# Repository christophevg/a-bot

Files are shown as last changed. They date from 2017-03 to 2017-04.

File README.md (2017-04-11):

# A-Bot
Een eigen kleine programmeerbare, zelf-rijdende robot maken.  
[http://knutselbaar.be/projecten/A-Bot](http://knutselbaar.be/projecten/A-Bot)

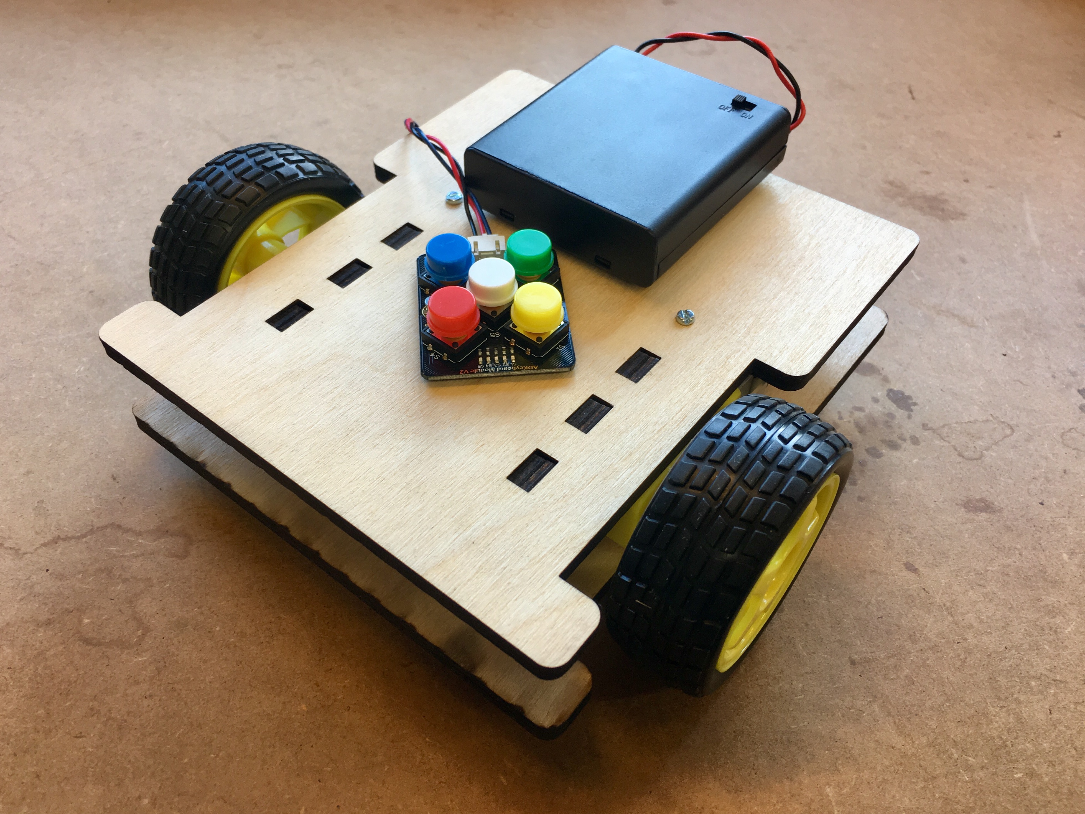
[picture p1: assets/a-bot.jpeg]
A-Bot

<p align="right">A-Bot versie 1</p>

## Inleiding

Tijdens een bezoek aan [Technolopis](http://technopolis.be) ontdekte onze zoon Arjen, 5 jaar, de [Bee Bot](https://www.bee-bot.us). Een zeer eenvoudige, programmeerbare, zelf-rijdende robot.

Via enkele knoppen kan deze robot geprogrammeerd worden om rond te rijden: rechtdoor, rechts/links draaien,... Op die manier kunnen kinderen eenvoudig leren om via elementaire ruimtelijke instructies de robot een parcours af te laten leggen.

Je kan deze bots kopen, voor ongeveer 80 euro, maar... je kan dit ook vrij eenvoudig zelf maken. Er bestaan zelfs veel kits van gelijkaardige robots, maar... je kan dit ook vrij eenvoudig zelf maken :-)

Dit project is bedoeld om te tonen hoe je dit kan doen en hoe je dus naast veel plezier met de robot zelf, ook heel veel plezier kan hebben om te leren hoe je dit zelf kan bouwen.

Er zijn verschillende aspecten aan: enerzijds de constructie van de robot en anderzijds de programmatie om hem echt tot leven te brengen.

### In deze _repository_

...verzamelen we alle bestanden, documenten, tekeningen, ontwerpen die we maken om de E-Liner te ontwerpen, alsook de software die we er op zetten om hem te laten rijden en te programmeren.

## Versie 1

### Onderdelen

Voor de eerste versie van de A-Bot vertrekken we van een [Particle Photon](https://www.particle.io/products/hardware/photon-wifi-dev-kit). Dit is een Arduino-achtige microcontroller met WiFi en een fantastisch online platform om er mee te werken.

Als aandrijving vertrekken we van een paar eenvoudige DC motoren. Om deze makkelijk aan te sturen, gebruiken we bijkomende chip: de L293. Om de motoren iets beter te kunnen controleren, voegen we ook een _encoder_ toe. 

Een balwiel, enkele knoppen en een batterijbox, maken onze onderdelen lijst compleet.

* 1 x [Particle Photon](https://www.antratek.be/photon) (~&euro;24)
* 1 x set [DC motoren en wielen](https://iprototype.nl/products/robotics/servo-motors/motors-wheels) (~&euro;18)
* 1 x [L293DNE](https://iprototype.nl/products/components/ics/motorcontroller-chip-L293D) (~&euro;5,15)
* 1 x set [Encoders voor DC motor](https://iprototype.nl/products/robotics/misc/dc-motor-encoder) (~&euro;15,50)
* 1 x [Gravity Keypad](https://iprototype.nl/products/components/buttons-switches/gravity-keypad) (~&euro;8)
* 1 x [Ball caster](https://iprototype.nl/products/robotics/misc/ball-caster-30mm) (~&euro;2,30)
* 1 x [Batterijbox 4xAA](https://iprototype.nl/products/accessoires/power/battery-box-4xAA) (~&euro;4,75)

### Chassis Design

Om al deze onderdelen samen te brengen tot een robotje, snijden we uit hout (of plexi) enkele delen met behulp van een laser cutter:

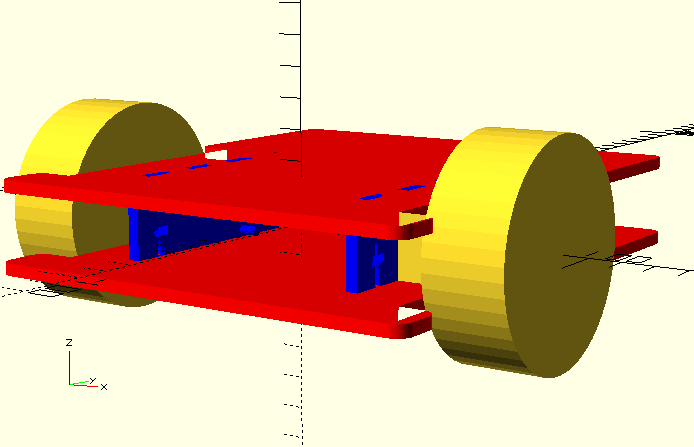
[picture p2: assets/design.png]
Design


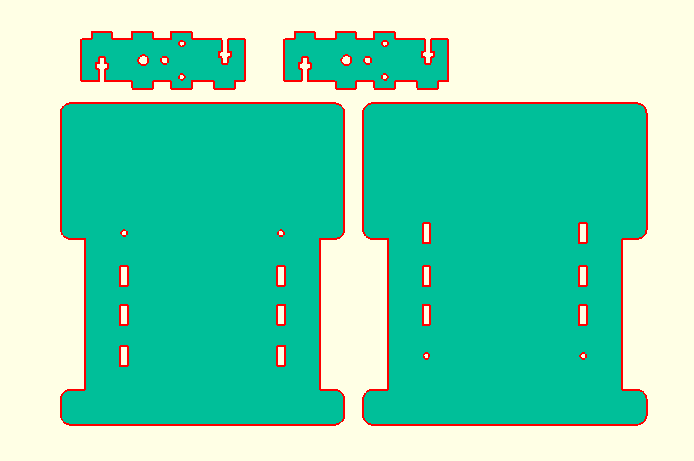
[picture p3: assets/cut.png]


### Electronica & Software

In verschillende stappen kan je zelf je A-Bot opbouwen:

1. [Blink](src/blink/) - Dit is de eenvoudigste test om te controleren dat alles werkt. Het laat de ingebouwde blauwe LED van de Photon blinken.
2. [Motor](src/motor/) - Dit is de basis opstelling voor het aansturen van een motor.
3. [Encoder](src/encoder/) - Dit is de basis opstelling voor het uitlezen van een encoder.
4. [Keypad](src/keypad/) - Dit is de basis opstelling voor het uitlezen van het keypad. 
5. [A-Bot](src/a-bot/) - Deze applicatie brengt alle onderdelen van de A-Bot samen tot een programmeerbaar robotje.

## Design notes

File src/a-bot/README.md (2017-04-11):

# A-Bot

Deze applicatie brengt alle onderdelen van de A-Bot samen tot een programmeerbaar robotje.

A-Bot

## Wat moet je bouwen?

Als we nu 2 [motoren](../motor/), 2 [encoders](../encoder/) en 1 [keypad](../keypad/) samenbrengen en zelf eventueel een _gaatjesprint_ maken, bekom je de volledige electronica die je nodig hebt:

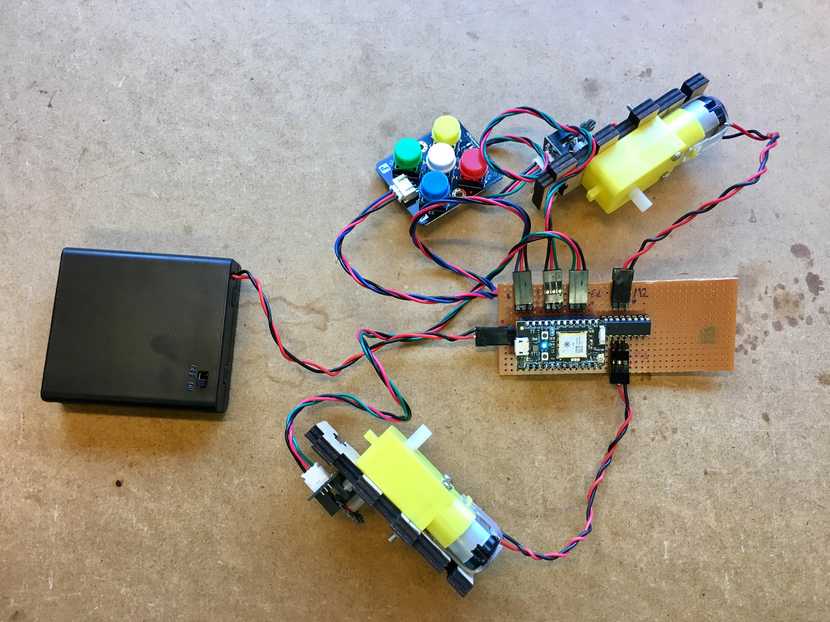
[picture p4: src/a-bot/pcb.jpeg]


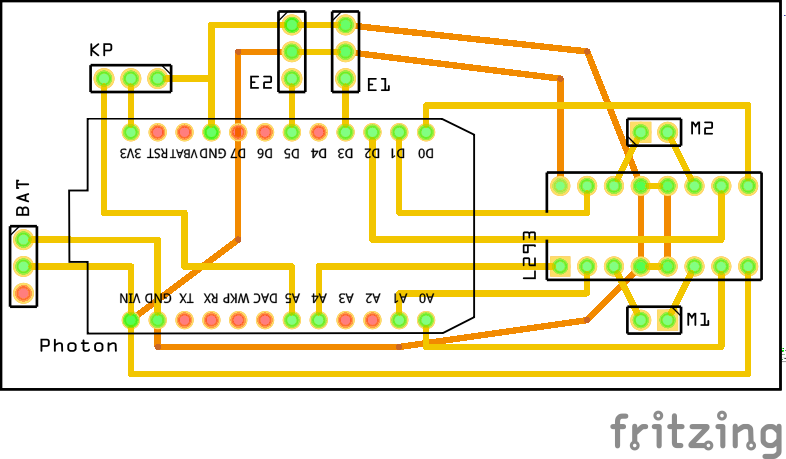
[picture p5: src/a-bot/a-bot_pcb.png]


Als je andere pinnen van de Photon gebruikt, kan je dit in [`config.h`](config.h) configureren.

## Hoe doe je dit werken op de Photon?

Vanuit de `src/` folder, geef je het commando `make`:

```bash
$ PROJECT=a-bot make
*** Compileren en flashen van a-bot
particle flash 2b002f001147333439313830 a-bot
Including:
    a-bot/config.h
    a-bot/a-bot.ino
attempting to flash firmware to your device 2b002f001147333439313830
Flash device OK:  Update started
*** Start van console uitvoer. Beëindig met 'Ctrl+a k y'.
    Druk op een toets om verder te gaan...
```

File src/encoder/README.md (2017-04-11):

# Encoder

Dit is de basis opstelling voor het uitlezen van een encoder.

## Wat moet je bouwen?

Dit voorbeeld bouwt voort op het voorbeeld voor de [motor](../motor/). Op de [wiki van DFRobot](https://www.dfrobot.com/wiki/index.php/Wheel_Encoders_for_DFRobot_3PA_and_4WD_Rovers_(SKU:SEN0038)) vind je informatie hoe je de encoder op de motor kan aansluiten.

De gebruikte motoren verschillen echter een beetje en vragen wat knutselwerk. De opstelling van het chassis laat echter toe om de encoder op de vertikale steunen te bevestigen nadat de motoren langs de andere kant van de steun bevestigd is.

(_foto's volgen_)

## Hoe werkt dit?

Een encoder bestaat uit een getand wieltje en een lichtsensor. Wanneer het wieltje met de as van de motor ronddraait zullen de tandjes het licht afwisselend doorlaten of tegenhouden.

De encoder vraagt een 5V voeding en geeft een digitaal signaal terug dat aangeeft of de encoder licht detecteert of niet. Zo kunnen we het aantal tandjes dat ronddraaien tellen.

## Hoe doe je dit werken op de Photon?

Vanuit de `src/` folder, geef je het commando `make`:

```bash
$ PROJECT=encoder make
*** Compileren en flashen van encoder
particle flash 2b002f001147333439313830 encoder
Including:
    encoder/encoder.ino
attempting to flash firmware to your device 2b002f001147333439313830
Flash device OK:  Update started
*** Start van console uitvoer. Beëindig met 'Ctrl+a k y'.
    Druk op een toets om verder te gaan...
```

Op de console toont de applicatie telkens het aantal stappen dat geteld werd gedurende 2 seconden.

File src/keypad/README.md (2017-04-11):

# Keypad

Dit is de basis opstelling voor het uitlezen van het keypad.

## Wat moet je bouwen?

De encoder wordt aangesloten met drie draden: 2 daarvan dienen voor de stroomvoorziening en de derde geeft een signaal terug dat aangeeft welke knop ingeduwd wordt.

Volgens de documentatie van het keypad, werkt dit op 5V. De Photon wordt wel gevoed met 5V, maar werkt voor de rest hoofdzakelijk op 3.3V. Als we naar de [samenstelling](https://iprototype.nl/docs/gravity-keypad-schema.pdf) van het keypad kijken, zien we dat de knoppen met verschillende weerstanden zorgen voor verschillende spanningen over de uitgaande, derde draad.

Voor dit voorbeeld, sluiten we het keypad dus aan op pinnen `3.3V`, `GND` en `A4`.

## Hoe werkt dit?

In de code bevindt zich 1 functie die de uitgaande spanning van het keypad leest en omzet tot een numerieke aanduiding voor de ingedrukte knop:

```c
#define KNOPPEN A4

uint8_t lees_knoppen() {
  int invoer = 4095 - analogRead(KNOPPEN);
  if(invoer < 200) { return 0; }
  if(invoer < 300) { return 5; }
  if(invoer < 500) { return 4; }
  if(invoer < 645) { return 1; }
  if(invoer < 675) { return 3; }
  if(invoer < 800) { return 2; }
  return 0; // geen knop
}
```

## Hoe doe je dit werken op de Photon?

Vanuit de `src/` folder, geef je het commando `make`:

```bash
$ PROJECT=keypad make
*** Compileren en flashen van keypad
particle flash 2b002f001147333439313830 keypad
Including:
    keypad/keypad.ino
attempting to flash firmware to your device 2b002f001147333439313830
Flash device OK:  Update started
*** Start van console uitvoer. Beëindig met 'Ctrl+a k y'.
    Druk op een toets om verder te gaan...
```

Op de console toont de applicatie de knoppen die ingedrukt worden.

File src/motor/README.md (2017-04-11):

# Motor

Dit is de basis opstelling voor het aansturen van een motor.

## Wat moet je bouwen?

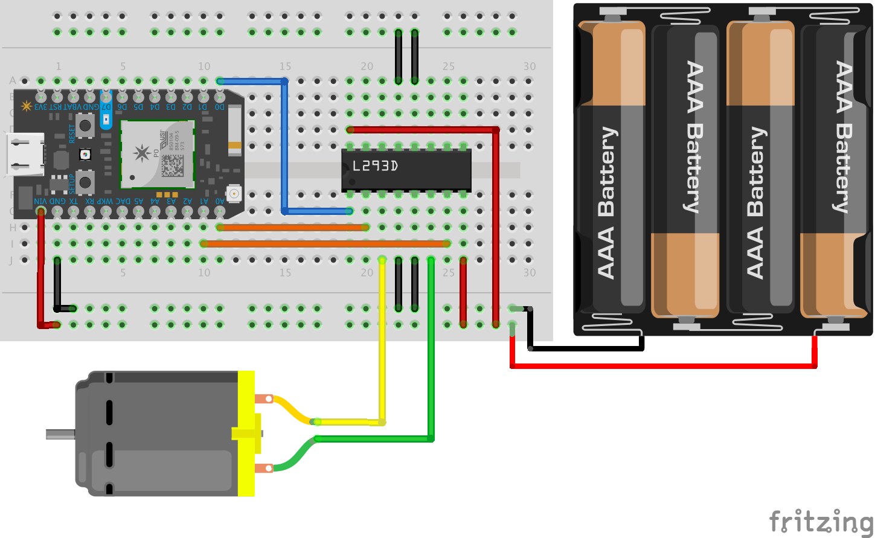
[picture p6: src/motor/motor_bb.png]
Breadboard


De batterijen voorzien de opstelling van iets meer dan 5V. Hiermee wordt (via de rode draden) enerzijds de Photon van stroom voorzien, als ook de L293D.

De L293D wordt aangestuurd met drie draden per motor: 2 draden dienen om de draai-richting aan te geven (oranje) en 1 draad om de snelheid te bepalen (blauw).

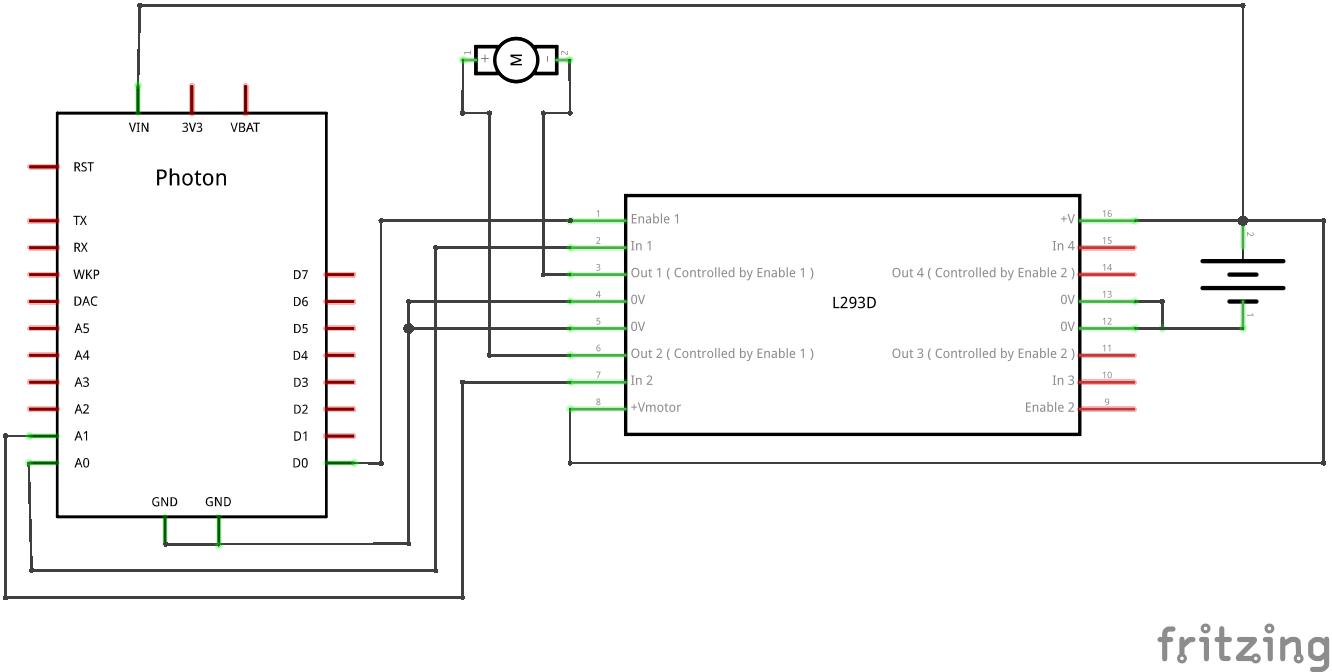
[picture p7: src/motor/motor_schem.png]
Schema


De twee draden waarmee we de draai-richting kunnen aangeven, kunnen samen 4 verschillende situaties aangeven: stilstaan, linksom draaien, rechtsom draaien en remmen.

## Software

In de software zie je één functie die alle logica bevat om een motor aan te sturen:

```c
void motor_update(int16_t snelheid) {
  // houd snelheid binnen grenzen
  if(abs(snelheid) < MIN_SNELHEID) { snelheid = 0; }
  if(abs(snelheid) > MAX_SNELHEID) {
    snelheid = MAX_SNELHEID * (snelheid/abs(snelheid));
  }

  // bepaal draairichting
  if(snelheid == 0) {
    // stop
    digitalWrite(MOTOR1_1A, LOW);
    digitalWrite(MOTOR1_2A, LOW);
  } else if(snelheid < 0) {
    // achterwaarts
    digitalWrite(MOTOR1_1A, HIGH);
    digitalWrite(MOTOR1_2A, LOW);
  } else {
    // voorwaarts
    digitalWrite(MOTOR1_1A, LOW);
    digitalWrite(MOTOR1_2A, HIGH);
  }
  // PWM
  analogWrite(MOTOR1_EN, abs(snelheid));
}
```

## Hoe doe je dit werken op de Photon?

Vanuit de `src/` folder, geef je het commando `make`:

```bash
$ PROJECT=motor make
*** Compileren en flashen van motor
particle flash 370026000447333436363331 motor
Including:
    /Users/xtof/Workspace/knutselbaar/a-bot/src/motor/motor.ino
attempting to flash firmware to your device 370026000447333436363331
Flash device OK:  Update started
*** Start van console uitvoer. Beëindig met 'Ctrl+a k y'.
    Druk op een toets om verder te gaan...
```

De uitvoer van de software toont de veranderingen van de snelheid van de motor:

```
60
80
100
120
140
160
180
200
220
240
260
280
-60
-80
-100
-120
-140
-160
-180
-200
-220
-240
-260
-280
```

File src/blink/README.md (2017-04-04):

# Blink

Dit is de eenvoudigste test om te controleren dat alles werkt. Het laat de ingebouwde blauwe LED van de Photon blinken.

## Hoe doe je dit werken op de Photon?

Vanuit de `src/` folder, geef je het commando `make`:

```bash
$ make
*** Compileren en flashen van blink
particle flash 370026000447333436363331 blink
Including:
    /Users/xtof/Workspace/knutselbaar/a-bot/src/blink/blink.ino
attempting to flash firmware to your device 370026000447333436363331
Flash device OK:  Update started
```

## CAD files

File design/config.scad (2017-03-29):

$fn = 50;

// vijzen, moeren en t-verbinding

vijs_diameter     = 3.1;
vijs_lengte       = 16 - 3;

moer_diameter     = 6.4;
moer_hoogte       = 3; 

// motor en wiel

motor_lengte      = 65;
motor_hoogte      = 22.3;
motor_breedte     = 18.5;

motor_as_lengte   = 38;
motor_as_diameter = 5.3;

motor_as_afstand_rand = motor_hoogte / 2;

motor_gat_afstand_voorkant = 30;
motor_gat_afstand_zijkant  = 0.75;
motor_gat_diameter         = 3.1;

motor_uitstulping_diameter   = 4;
motor_uitstulping_afstand_as = 11.275;

wiel_breedte      = 26;
wiel_diameter     = 70;
wiel_as_breedte   = 30;
wiel_as_diameter  = 14;

// chassis

chassis_lengte    = 170;
chassis_breedte   = 150;
chassis_dikte     = 4;
chassis_afronding = 5;

wiel_uitsparing   = wiel_diameter + chassis_afronding * 2 + 10;

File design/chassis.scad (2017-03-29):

include <config.scad>

module t(dikte=1) {
  union() {
    translate([-vijs_diameter/2,0,0]) {
      cube([vijs_diameter, vijs_lengte, dikte]);
    }
    translate([-moer_diameter/2, vijs_lengte/2,0]) {
      cube([moer_diameter, moer_hoogte, dikte]);
    }
  }
}

// t();

// TODO: plaats motor in XY vlak met assen in Z vlak, zodat snijdingen zonder
//       rotaties mogelijk zijn.

module motor() {
  // motorblok
  translate([0, -motor_as_afstand_rand, -motor_as_afstand_rand]) {
    cube([motor_breedte, motor_lengte, motor_hoogte]);
  }
  // as
  translate([-(motor_as_lengte - motor_breedte)/2, 0, 0]) {
    rotate([0,90,0]) { cylinder(motor_as_lengte, d=motor_as_diameter); }
  }
  // gaten (voorgesteld als staven/vijzen)
  translate([
    0,
    -motor_as_afstand_rand+motor_gat_diameter/2+motor_gat_afstand_voorkant,
    -motor_as_afstand_rand+motor_gat_diameter/2+motor_gat_afstand_zijkant,
  ]) {
    rotate([0,90,0]) { cylinder(motor_breedte+10, d=motor_gat_diameter); }
  }
  translate([
    0,
    -motor_as_afstand_rand+motor_gat_diameter/2+motor_gat_afstand_voorkant,
    +motor_as_afstand_rand-motor_gat_diameter/2-motor_gat_afstand_zijkant,
  ]) {
    rotate([0,90,0]) { cylinder(motor_breedte+10, d=motor_gat_diameter); }
  }
  // gat voor "uitstulping"
  translate([ 0, motor_uitstulping_afstand_as, 0 ]) {
    rotate([0,90,0]) { cylinder(motor_breedte+10, d=motor_uitstulping_diameter); }
  }
}

module wiel() {
  cylinder(wiel_breedte,    d=wiel_diameter);
  cylinder(wiel_as_breedte, d=wiel_as_diameter);
}

module motor_met_wiel() {
  translate([-wiel_as_breedte,0,0]) { rotate([0, 90, 0]) { wiel(); } }
  motor();
}

// motor_met_wiel();

// door de afronding, wordt het chassis groter. deze hulp-variabelen zijn de 
// netto waarden.
breedte = chassis_breedte / 2 - chassis_afronding;
lengte  = chassis_lengte - 2 * chassis_afronding;
dikte   = chassis_dikte / 2; // later bij afronding komt dit er terug bij

// het chassis is symmertrisch, dus we kunnen een half chassis modelleren en dan
// tweemaal naast elkaar plaatsen om een heel chassis te bekomen.
module half_chassis() {
  difference() {
    // half chassis
    cube([ breedte, lengte, dikte ]);
    // uitsparing voor wiel op 1/3 van voorkant, halve wiel breedte diep
    translate([0, (lengte/3)-(wiel_uitsparing/2), 0]) {
      cube([wiel_breedte/2, wiel_uitsparing, dikte]);
    }
  }
}

module motor_steun() {

  module vleugel() { cube([motor_lengte/6, chassis_dikte, chassis_dikte]); }

  difference() {
    union() {
      translate([-motor_lengte/6*2,0,0]) {
        cube([motor_lengte+motor_lengte/6*2, motor_hoogte, chassis_dikte]);
      }
      // vleugels bovenkant
      translate([ motor_lengte/6*-1.5,  motor_hoogte,  0 ]) { vleugel(); }
      translate([ motor_lengte/6*0.5,  motor_hoogte,  0 ]) { vleugel(); }
      translate([ motor_lengte/6*2.4,  motor_hoogte,  0 ]) { vleugel(); }
      // vleugels onderkant
      translate([ motor_lengte/6*0.5, -chassis_dikte, 0 ]) { vleugel(); }
      translate([ motor_lengte/6*2.4, -chassis_dikte, 0 ]) { vleugel(); }
      translate([ motor_lengte/6*4.5, -chassis_dikte, 0 ]) { vleugel(); }
    }
    // t-verbindingen bovenkant
    translate([motor_lengte/6*5, motor_hoogte, 0]) {
      mirror([0,1,0]) { t(chassis_dikte); }
    }
    // // t-verbindingen onderkant
    translate([motor_lengte/6*-1, 0, 0]) {
      t(chassis_dikte);
    }

    translate([motor_as_afstand_rand,motor_as_afstand_rand,-motor_breedte]) { rotate([0,-90,-90]) { motor(); } }
  }
}

// motor_steun();

// Deze module wordt alleen gebruikt om de uitsparingen in de platen te maken.
// Normaal gezien zouden we hiervoor gewoon de module van de steun zelf
// gebruiken. Zie https://github.com/openscad/openscad/issues/1974 voor meer
// info omtrent wat waarschijnlijk een bug is. Het probleem lijkt verbonden aan
// rotatie, dus deze module implementeert de rotatie "manueel".

module motor_steun_vleugels() {

  module vleugel() { cube([chassis_dikte, motor_lengte/6, chassis_dikte]); }

  // vleugels bovenkant
  translate([0, motor_lengte/6*-1.5, motor_hoogte])  { vleugel(); }
  translate([0, motor_lengte/6*0.5,  motor_hoogte])  { vleugel(); }
  translate([0, motor_lengte/6*2.4,  motor_hoogte])  { vleugel(); }
  // vleugels onderkant
  translate([0, motor_lengte/6*0.5, -chassis_dikte]) { vleugel(); }
  translate([0, motor_lengte/6*2.4, -chassis_dikte]) { vleugel(); }
  translate([0, motor_lengte/6*4.5, -chassis_dikte]) { vleugel(); }
  
  module vijs() { cylinder(d=vijs_diameter, h=vijs_lengte); }
  
  // vijzen
  translate([chassis_dikte/2, 0, 0]) {        // midden dikte steun
    // boven
    translate([0, 0, motor_hoogte+chassis_dikte-vijs_lengte]) {  // door plaat
      translate([0, motor_lengte/6*5, 0]) { vijs(); }
    }
    // onder
    translate([0, 0, -chassis_dikte]) {       // door plaat
      translate([0, motor_lengte/6*-1, 0]) { vijs(); }
    }
  }
}

// motor_steun_vleugels();

module afgeronde_plaat() {
  // gecentreerd op middelpunt van wiel-as van robot
  translate([-breedte, -lengte/3, 0 ]) {
    minkowski() {
      union() {
        half_chassis();
        translate([chassis_breedte-2*chassis_afronding, 0, 0]) {
          mirror([1,0,0]) { half_chassis(); }
        }
      }
      cylinder(r=chassis_afronding, h=dikte);
    }
  }
}

// afgeronde_plaat();

module plaat_boven() {
  difference() {
    afgeronde_plaat();
    // uitsparingen voor wiel-steunen
    translate([
      -(chassis_breedte/2 - wiel_breedte/2 - motor_breedte),
      -motor_as_afstand_rand,
      -motor_hoogte
    ]) {
      motor_steun_vleugels();
    }
    translate([
      chassis_breedte/2 - wiel_breedte/2 - motor_breedte - chassis_dikte,
      -motor_as_afstand_rand,
      -motor_hoogte
    ]) {
      motor_steun_vleugels();
    }
  }
}

// plaat_boven();

module plaat_onder() {
  difference() {
    afgeronde_plaat();
    // uitsparingen voor wiel-steunen
    translate([
      -(chassis_breedte/2 - wiel_breedte/2 - motor_breedte),
      -motor_as_afstand_rand,
      chassis_dikte
    ]) {
      motor_steun_vleugels();
    }
    translate([
      chassis_breedte/2 - wiel_breedte/2 - motor_breedte - chassis_dikte,
      -motor_as_afstand_rand,
      chassis_dikte
    ]) {
      motor_steun_vleugels();
    }
  }
}

// plaat_onder();

module demo() {
  translate([-(chassis_breedte/2-wiel_breedte/2),0,0]) { motor_met_wiel(); }
  translate([chassis_breedte/2-wiel_breedte/2, 0, 0]) {
    mirror([1, 0, 0]) { motor_met_wiel(); }
  }

  translate([0,0, motor_as_afstand_rand]) {
    color("red") { plaat_boven(); }
  }
  translate([0,0,-(motor_as_afstand_rand+chassis_dikte)]) {
    color("red") { plaat_onder(); }
  }
  color("blue") {
    translate([
      -(chassis_breedte/2-wiel_breedte/2-motor_breedte),
      -motor_as_afstand_rand,
      -motor_as_afstand_rand,
    ]) {
      rotate([90,0,90]) { motor_steun(); }
    }
    translate([
      chassis_breedte/2-wiel_breedte/2-motor_breedte-chassis_dikte,
      -motor_as_afstand_rand,
      -motor_as_afstand_rand,
    ]) {
      rotate([90,0,90]) { motor_steun(); }
    }
  }
}

demo();

$vpt = [ 8.88, 12.71, 27.73 ];
$vpr = [ 83.30, 0.00, 34.30 ];
$vpd = 500;

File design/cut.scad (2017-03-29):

include <config.scad>
use <chassis.scad>

spacing = 10;

projection(cut = true) {
  plaat_boven();
  translate([chassis_breedte + spacing,0,0]) { plaat_onder(); }
  translate([0,0,-0.1]) {    // TEMP: fix issue after rotation of motor
    translate([-motor_lengte/6*3 - spacing, chassis_lengte/3*2 + spacing, 0]) {
      motor_steun();
    }
    translate([motor_lengte, chassis_lengte/3*2 + 10, 0]) {
      motor_steun();
    }
  }
}

$vpt = [ 76.46, 62.66, 30.14 ];
$vpr = [ 0.00, 0.00, 0.00 ];
$vpd = 800;

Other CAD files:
design/test.scad

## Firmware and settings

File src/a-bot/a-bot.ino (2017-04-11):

// dit is de applicatie voor de (hele) A-Bot
// auteur: Christophe VG <contact@christophe.vg>

#include "config.h"

void setup() {
  Serial.begin(9600);

  // motoren 1 & 2
  pinMode(MOTOR1.en, OUTPUT);
  pinMode(MOTOR1.h1, OUTPUT);
  pinMode(MOTOR1.h2, OUTPUT);

  pinMode(MOTOR2.en, OUTPUT);
  pinMode(MOTOR2.h1, OUTPUT);
  pinMode(MOTOR2.h2, OUTPUT);

  // encoders 1 & 2
  attachInterrupt(ENCODER1, encoder1_verandering, CHANGE);
  attachInterrupt(ENCODER2, encoder2_verandering, CHANGE);
}

void motor_update(motor_t motor, int16_t snelheid) {
  // houd snelheid binnen grenzen
  if(abs(snelheid) < MIN_SNELHEID) { snelheid = 0; }
  if(abs(snelheid) > MAX_SNELHEID) {
    snelheid = MAX_SNELHEID * (snelheid/abs(snelheid));
  }

  Serial.print(motor.en); Serial.print( " = " ); Serial.println(snelheid);

  // PWM
  analogWrite(motor.en, abs(snelheid));

  // bepaal draairichting
  if(snelheid == 0) {
    digitalWrite(motor.h1, HIGH);
    digitalWrite(motor.h2, HIGH);
    delay(50);
    // stop
    digitalWrite(motor.h1, LOW);
    digitalWrite(motor.h2, LOW);
  } else if(snelheid < 0) {
    // achterwaarts
    digitalWrite(motor.h1, HIGH);
    digitalWrite(motor.h2, LOW);
  } else {
    // voorwaarts
    digitalWrite(motor.h1, LOW);
    digitalWrite(motor.h2, HIGH);
  }
}

// encoders
volatile uint16_t stappen1 = 0;
volatile uint16_t stappen2 = 0;

void encoder1_verandering() {
  stappen1++;
}

void encoder2_verandering() {
  stappen2++;
}

// keypad
// s1    s2     s3      s4     s5
//   600    650    700     800    900
uint8_t lees_knoppen() {
  int invoer = 4095 - analogRead(KNOPPEN);
  if(invoer < 200) { return 0; }
  if(invoer < 300) { return 5; }
  if(invoer < 500) { return 4; }
  if(invoer < 645) { return 1; }
  if(invoer < 675) { return 3; }
  if(invoer < 800) { return 2; }
  return 0; // geen knop
}

// hulp functies

uint16_t doel1 = 0;
uint16_t doel2 = 0;

void vooruit() {
  stappen1 =  0;
  stappen2 =  0;
  doel1    = STAPPEN_RECHT;
  doel2    = STAPPEN_RECHT;
  motor_update(MOTOR1,  SNELHEID);
  motor_update(MOTOR2, -SNELHEID);
}

void links() {
  stappen1 =  0;
  stappen2 =  0;
  doel1    = STAPPEN_DRAAI;
  doel2    = STAPPEN_DRAAI;
  motor_update(MOTOR1,  SNELHEID);
  motor_update(MOTOR2,  SNELHEID);
}

void rechts() {
  stappen1 =  0;
  stappen2 =  0;
  doel1    = STAPPEN_DRAAI;
  doel2    = STAPPEN_DRAAI;
  motor_update(MOTOR1, -SNELHEID);
  motor_update(MOTOR2, -SNELHEID);
}

void achteruit() {
  stappen1 =  0;
  stappen2 =  0;
  doel1    = STAPPEN_RECHT;
  doel2    = STAPPEN_RECHT;
  motor_update(MOTOR1, -SNELHEID);
  motor_update(MOTOR2,  SNELHEID);
}

void stop() {
  stappen1 = 0;
  stappen2 = 0;
  doel1    = 0;
  doel2    = 0;
  motor_update(MOTOR1, 0);
  motor_update(MOTOR2, 0);
}

// bediening

uint8_t vorige_knop = 0;
bool rijden = false;

void loop() {
  if(rijden) {
    loop_rijden();
  } else {
    loop_stilstaan();
  }
  delay(100);
}

uint8_t programma[255];
uint8_t pc = 0;

void stap() {
  Serial.print("stap ");
  Serial.print(pc); Serial.print(" = "); Serial.println(programma[pc]);
  
  rijden = true;
  switch(programma[pc]) {
    case 4: vooruit();   break;
    case 3: rechts();    break;
    case 2: achteruit(); break;
    case 1: links();     break;
    case 5:
      pc = 0;
      rijden = false;
      break;
  }
}

void loop_rijden() {
  uint8_t knop = lees_knoppen();

  // manueel onderbreken van het rijden
  if(knop != vorige_knop) {
    Serial.println("STOP!");
    stop();         // van zodra een knop aangeraakt wordt, stoppen we
    if(knop == 0) { // als de knop los gelaten is, gaan we over naar stilstaan
      rijden = false;
    }
    vorige_knop = knop;
    return;
  }

  // rijden tot doel bereikt is
  if(doel1 > 0 && stappen1 >= doel1) { motor_update(MOTOR1, 0); doel1 = 0; }
  if(doel2 > 0 && stappen2 >= doel2) { motor_update(MOTOR2, 0); doel2 = 0; }
  
  // normaal einde van het rijden, volgende stap
  if(doel1 == 0 && doel2 == 0) {
    pc++;
    stap();
  }
}

void loop_stilstaan() {
  uint8_t knop = lees_knoppen();

  if(knop != vorige_knop) {
    if(knop == 0) { // pas als de knop losgelaten wordt, starten we
      Serial.print(pc); Serial.print(" = "); Serial.println(vorige_knop);
      programma[pc++] = vorige_knop;
      if( vorige_knop == 5 ) {
        Serial.println("start...");
        pc = 0;
        stap();
      }
    }
    vorige_knop = knop;
  }
}

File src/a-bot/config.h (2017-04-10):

// configuratie van de a-bot
// author: Christophe VG <contact@christophe.vg>

#ifndef __CONFIG_H
#define __CONFIG_H

typedef struct {
  uint16_t en;
  uint16_t h1;
  uint16_t h2;
} motor_t;

// motoren 1 & 2
#define MOTOR1 (motor_t){ .en = A4, .h1 = A1, .h2 = A0 }
#define MOTOR2 (motor_t){ .en = D0, .h1 = D2, .h2 = D1 }

#define MIN_SNELHEID  160      // dit is de minimale snelheid = ~3V (van 5V)
#define MAX_SNELHEID  255      // dit is de maximale snelheid = ~3.5V (van 5V)

#define SNELHEID      MIN_SNELHEID

// encoders 1 & 2
#define ENCODER1      D3
#define ENCODER2      D5

#define STAPPEN_RECHT 53       // aantal stappen voor rechtdoor
#define STAPPEN_DRAAI 10       // aantal stappen voor kwart draai

// keypad
#define KNOPPEN       A5

#endif

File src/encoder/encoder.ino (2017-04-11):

// deze app laat een motor draaien en telt via de encoder de stappen
// auteur: Christophe VG <contact@christophe.vg>

#define MOTOR1_EN    D0      // dit controleert of de motor in gebruik is
#define MOTOR1_1A    A0      // dit controleert de draairichting
#define MOTOR1_2A    A1      // dit controleert de draairichting

#define ENCODER      D2

void setup() {
  Serial.begin(9600);
  pinMode(MOTOR1_EN, OUTPUT);
  pinMode(MOTOR1_1A, OUTPUT);
  pinMode(MOTOR1_2A, OUTPUT);
  
  attachInterrupt(ENCODER, encoder_verandering, CHANGE);
}

void motor_start() {
  digitalWrite(MOTOR1_EN, HIGH);
  digitalWrite(MOTOR1_1A, HIGH);
  digitalWrite(MOTOR1_2A, LOW);
}

void motor_stop() {
  digitalWrite(MOTOR1_EN, LOW);
  digitalWrite(MOTOR1_1A, LOW);
  digitalWrite(MOTOR1_2A, LOW);
}

volatile uint16_t stappen = 0;

void encoder_verandering() {
  stappen++;
}

void loop() {
  stappen = 0;
  motor_start();
  delay(2000);
  motor_stop();
  Serial.println(stappen);

  delay(2000);
}

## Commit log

2017-03-27 motor + wiel gemodelleerd
    [chassis.scad]
2017-03-27 eerste design gemodelleerd
    [chassis.scad, config.scad, cut.scad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]
2017-03-27 voorlopige BOM toegevoegd
2017-03-29 motor steun vergroot + montage-gaten toegevoegd
    [chassis.scad, config.scad, cut.scad]
2017-04-06 voorbeeld voor aansturing van een motor toegevoegd
    [motor.fzz]
2017-04-07 vereenvoudigde opstelling zonder mosfet
    [motor.fzz]
2017-04-07 voorbeeld voor encoder toegevoegd
2017-04-07 tijdelijke correcte README pagina voor encoder
2017-04-10 eerste echte A-Bot code toegevoegd
    [a-bot.fzz]
